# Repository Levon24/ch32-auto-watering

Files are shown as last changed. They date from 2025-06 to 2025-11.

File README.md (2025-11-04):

# ch32-auto-watering
Hello, the goal of this project was to create an automatic watering system for indoor plants using inexpensive and readily available components that can be ordered on AliExpress for final production. The system is based on the CH32v003 SoC, the most common board without a quartz crystal (at the time of writing, it costs 0.5$).
Here is device photo.
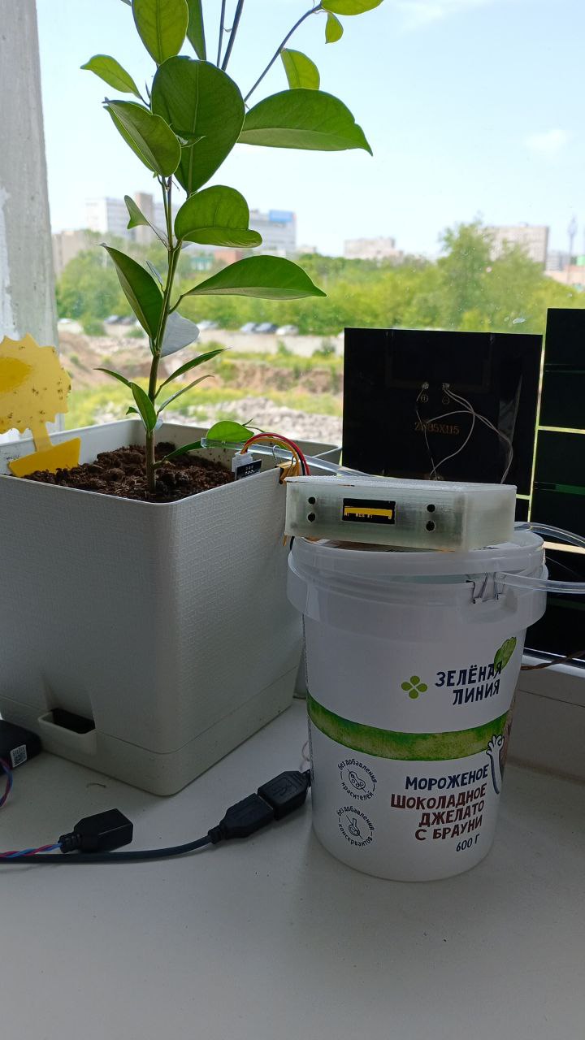
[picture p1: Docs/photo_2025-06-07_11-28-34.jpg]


## Electrical schema
The device's electrical circuit uses ready-made blocks, including a key for controlling the automatic irrigation pump. It would be better to build it using a modern element base of field-effect transistors. However, I had a lot of Soviet transistors, such as the KT601, KT602, and KT815, which I used to assemble the key for controlling the pump.
Here is main electrical schema.
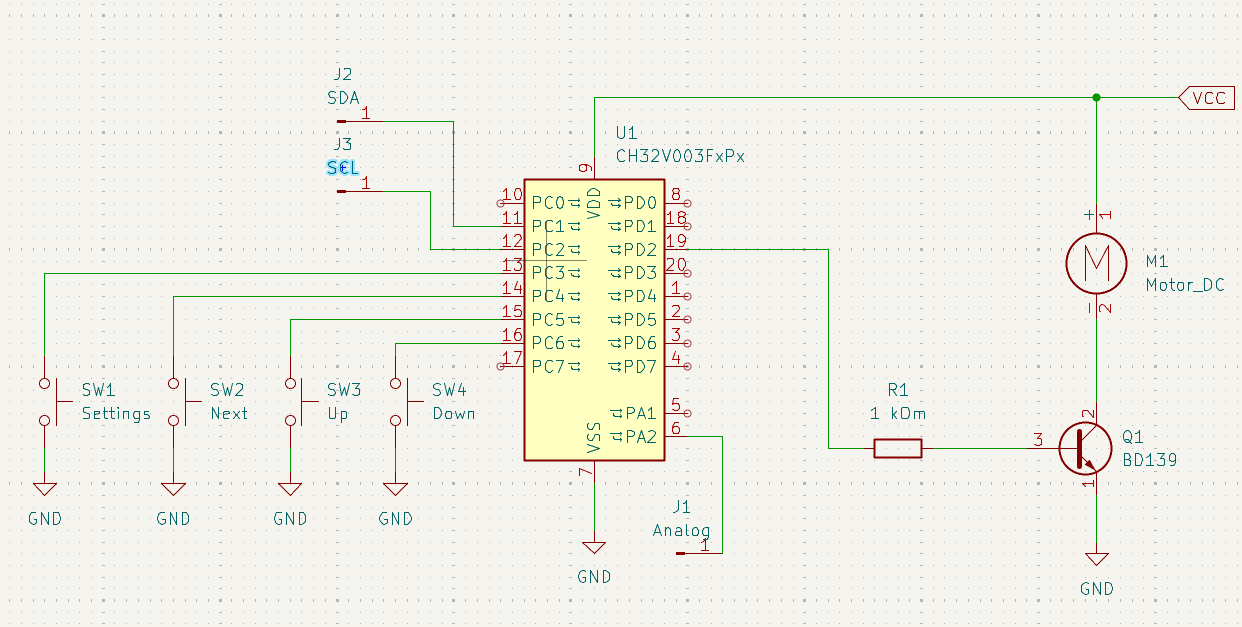
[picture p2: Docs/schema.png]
schema


As you can see in the image below, most of the prototype device is surface mounted and is not yet finished, as the project is still being refined.
Here is main block.
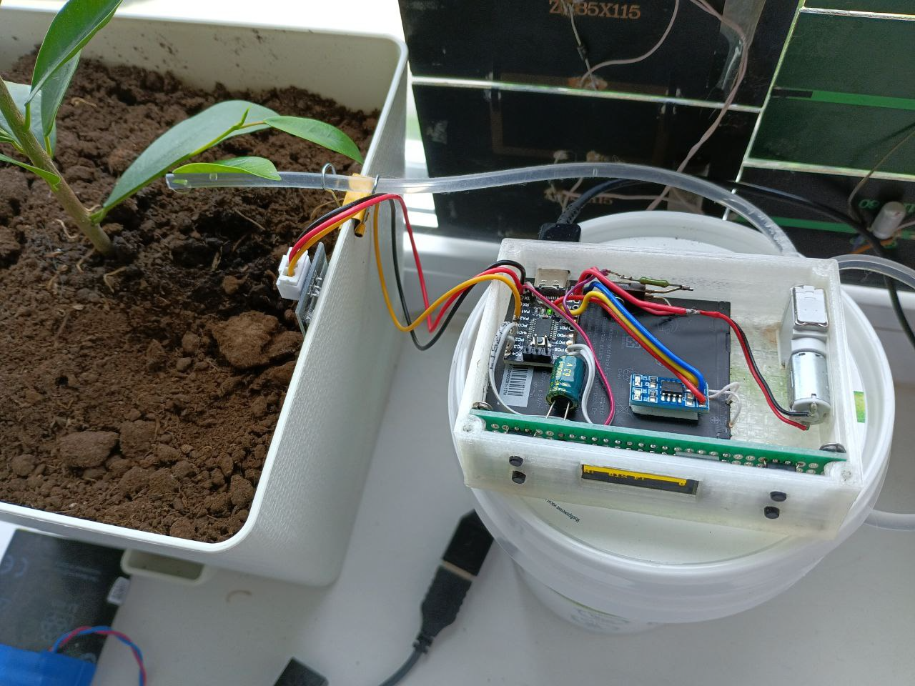
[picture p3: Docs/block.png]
block


### Soil moisture sensor
Initially, I used a common resistive soil moisture sensor for the device and, as shown in the diagram above, fed the signal to the ADC input. It was convenient for measuring data, from 0 V to a supply voltage of 3.3 V. The controller has a 10-bit ADC, so the values ranged from 0 to 1023 and were easy to convert to moisture percentages. However, something went wrong and the sensor malfunctioned.
Here is result.
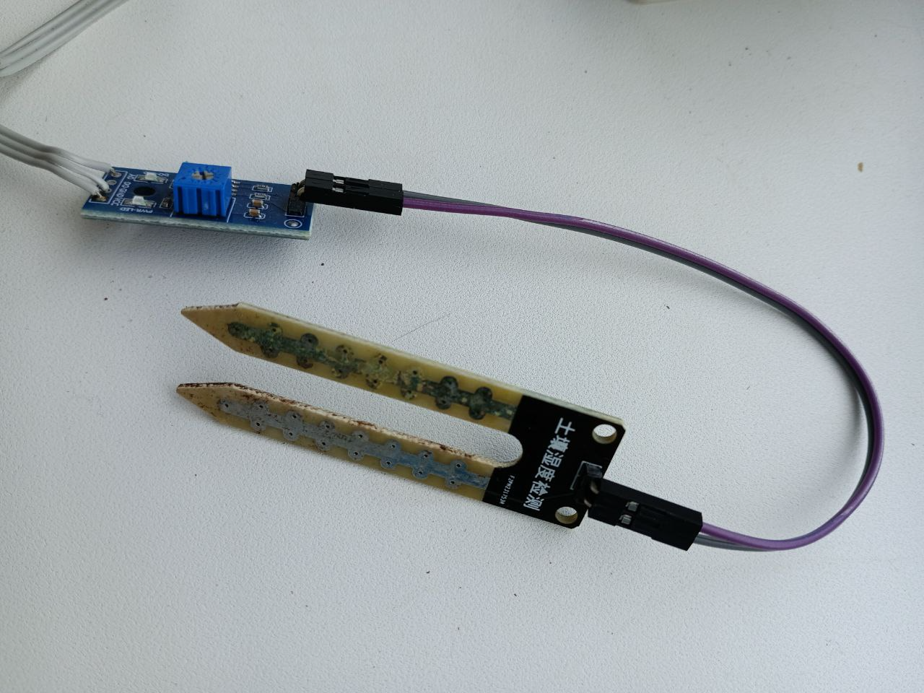
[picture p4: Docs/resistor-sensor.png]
resistor-sensor


The process of sensor electrode oxidation, as it turns out, is well-known. So, the solution is - using capacitive sensors.
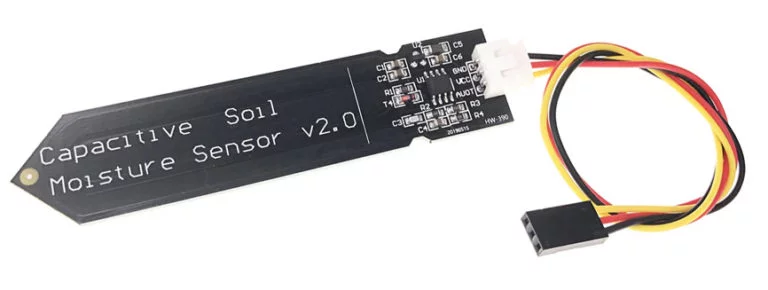
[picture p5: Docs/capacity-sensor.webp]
capacity-sensor


### Oled display
To display the data, I chose an OLED display with a 128x32 resolution. It displays current readings and a moisture graph over time. A target soil moisture value can be specified in the settings. The display shows two parameters: M (soil moisture) and F (flood value). The display itself is connected via two wires and operates using the I2C protocol.
The price of oled display 1$.
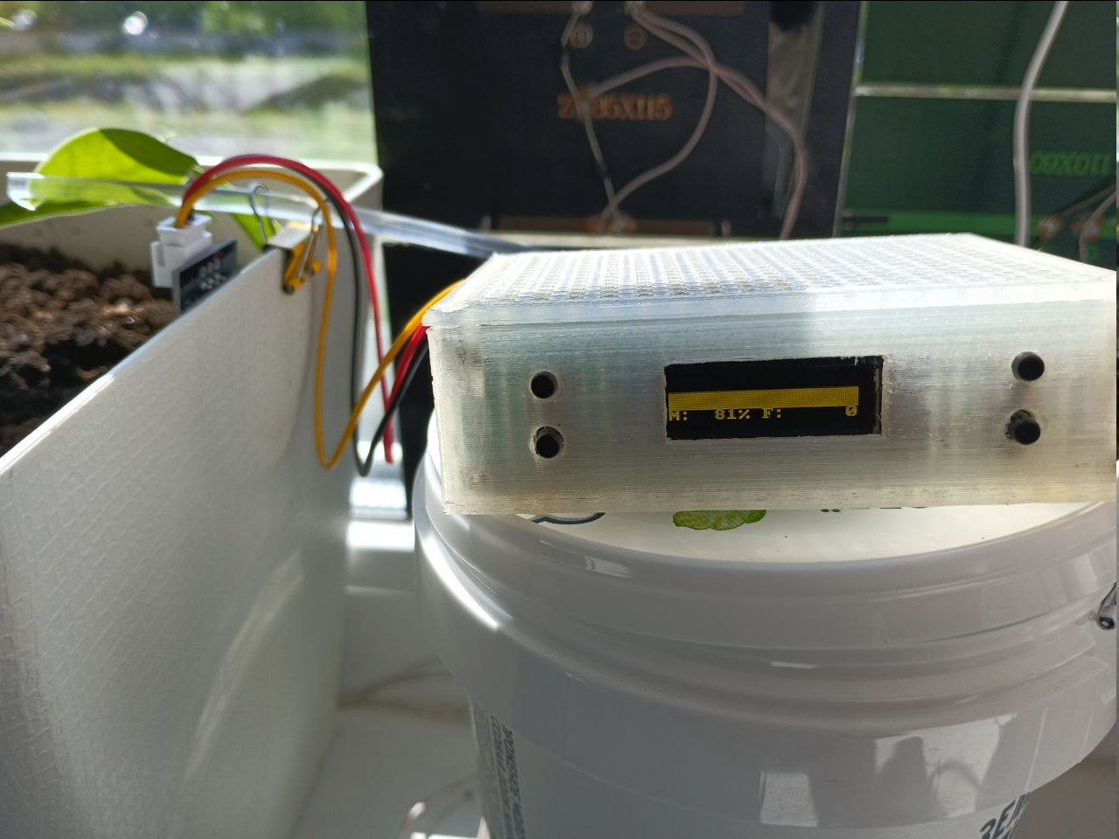
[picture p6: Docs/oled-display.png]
oled-display


### Pump
So, if the soil moisture is insufficient, the device begins to continuously dispense water until a set time threshold is reached, or until the soil reaches the desired moisture level. The time threshold is configured in the source code. I used the smallest **CJWP08** pump, which costs about 0.5$, so I set the threshold to 30 seconds of continuous watering. The pump then switches to drip mode, releasing a drop of water every set time until the desired moisture level is reached.

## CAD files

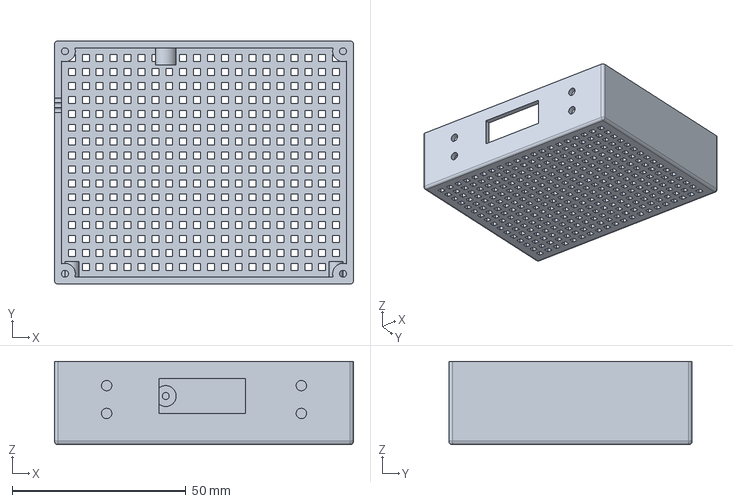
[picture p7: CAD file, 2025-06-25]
Docs/box.FCStd
86.0 x 70.0 x 24.0 mm

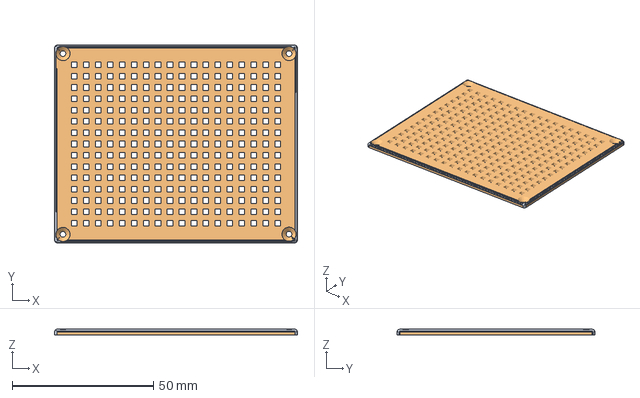
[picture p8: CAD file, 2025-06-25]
Docs/lid.FCStd
86.0 x 70.0 x 2.00 mm
MultiTransform (Meshed)

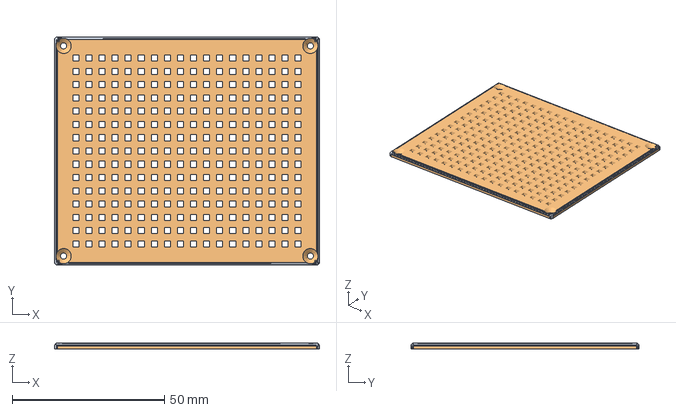
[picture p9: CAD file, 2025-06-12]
Docs/lid2.FCStd
87.0 x 75.0 x 2.00 mm
Body (Meshed)

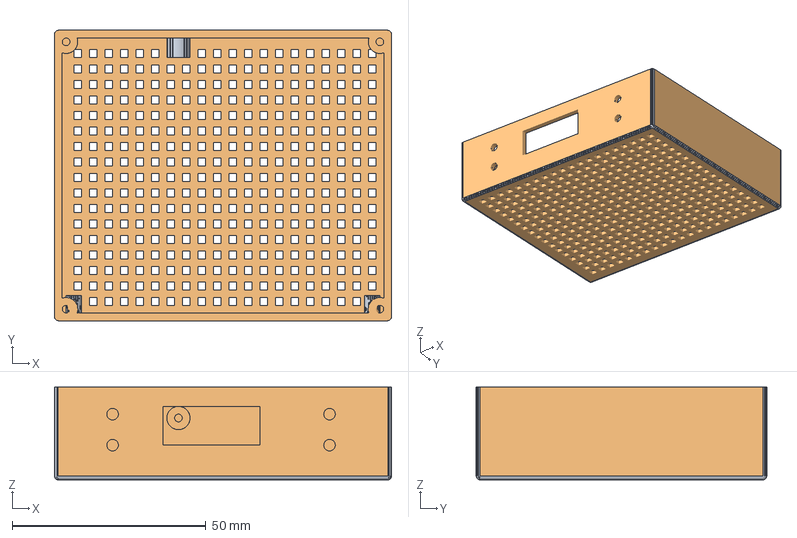
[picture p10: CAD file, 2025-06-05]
Docs/box2.FCStd
87.0 x 75.0 x 24.0 mm
Pad002 (Meshed)

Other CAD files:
Docs/box.stl
Docs/box2.stl
Docs/lid.stl
Docs/lid2.stl

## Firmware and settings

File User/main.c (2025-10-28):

#include "debug.h"
#include "display.h"
#include "fonts.h"
#include "buttons.h"

#define _TIM2_PSC   ((SystemCoreClock / 1000) - 1)
#define _TIM2_ARR   (1000 - 1)

#define SENSOR_CAP      1 // Емкостной датчик?
#define SENSOR_PIN      GPIO_Pin_0
#define PUMP_PIN        GPIO_Pin_2
#define MOISTURE        80 // Цель для влажности почвы
#define DELAY_MS        50 // Задержка в основном цикле, 20 кадров в секунду
#define FLOOD_STEP      5  // Сколько за шаг полива добавлять в счетчик потопа
#define FLOOD_MAX       (30 * FLOOD_STEP * 1000) / DELAY_MS // 30 секунд максимум лить воду до потопа
#define CHART_SECONDS   5  // Через сколько секунд график сдвигать вправо
#define CHART_SIZE      8 * 3
#define CHART_MAX       10
#define U_VREF          1.2 // 1.2V 
#define U_VCC           3.3 // 3.3V
#define U_DRY           2.26 // Калибровка для емкостного датчика 0 влажности (для v1.2 = 2.193, для v2.0 = 2.752)
#define U_WET           1.10 // Калибровка для емкостного датчика 100 влажности (для v1.2 = 1.06, для v2.0 = 1.304)

uint8_t seconds = 0;
uint8_t displayLine[128];
uint8_t chartValues[128];

extern enum display_state state;
extern enum display_setup setup;
extern _button_t buttons[BUTTONS];

extern const uint8_t font8x8[][8];
const uint8_t levels[] = {0b00000000, 0b10000000, 0b11000000, 0b11100000, 0b11110000, 0b11111000, 0b11111100, 0b11111110, 0b11111111};

uint8_t contrast = DISPLAY_DEFAULT_CONTRAST;
uint8_t moisture = 0;
uint8_t minMoisture = MOISTURE;
uint16_t flood = 0;

/**
 * @brief Init Port A
 */
void initPortA() {
  RCC_APB2PeriphClockCmd(RCC_APB2Periph_GPIOA, ENABLE);

  GPIO_InitTypeDef initTypeDef = {0};
  initTypeDef.GPIO_Pin = SENSOR_PIN;
  initTypeDef.GPIO_Mode = GPIO_Mode_AIN;
  GPIO_Init(GPIOA, &initTypeDef);
}

/**
 * @brief Init Port C
 */
void initPortC() {
  RCC_APB2PeriphClockCmd(RCC_APB2Periph_GPIOC, ENABLE);
  
  GPIO_InitTypeDef initI2C = {0};
  initI2C.GPIO_Pin = GPIO_Pin_1 | GPIO_Pin_2;
  initI2C.GPIO_Mode = GPIO_Mode_AF_OD;
  initI2C.GPIO_Speed = GPIO_Speed_30MHz;
  GPIO_Init(GPIOC, &initI2C);

  GPIO_InitTypeDef initButtons = {0};
  initButtons.GPIO_Pin = BUTTON_SETTINGS | BUTTON_NEXT | BUTTON_UP | BUTTON_DOWN;
  initButtons.GPIO_Mode = GPIO_Mode_IPU;
  initButtons.GPIO_Speed = GPIO_Speed_30MHz;
  GPIO_Init(GPIOC, &initButtons);
}

/**
 * @brief Init Port D
 */
void initPortD() {
  RCC_APB2PeriphClockCmd(RCC_APB2Periph_GPIOD, ENABLE);

  GPIO_InitTypeDef initTypeDef = {0};
  initTypeDef.GPIO_Pin = PUMP_PIN;
  initTypeDef.GPIO_Mode = GPIO_Mode_Out_PP;
  initTypeDef.GPIO_Speed = GPIO_Speed_30MHz;
  GPIO_Init(GPIOD, &initTypeDef);
}

/**
 * @brief Init I2C
 */
void initI2C() {
  RCC_APB1PeriphClockCmd(RCC_APB1Periph_I2C1, ENABLE);

  I2C_InitTypeDef initTypeDef = {0};
  initTypeDef.I2C_ClockSpeed = DISPLAY_I2C_SPEED;
  initTypeDef.I2C_Mode = I2C_Mode_I2C;
  initTypeDef.I2C_DutyCycle = I2C_DutyCycle_2;
  initTypeDef.I2C_OwnAddress1 = 0x00;
  initTypeDef.I2C_Ack = I2C_Ack_Enable;
  initTypeDef.I2C_AcknowledgedAddress = I2C_AcknowledgedAddress_7bit;
  I2C_Init(I2C1, &initTypeDef);

  I2C_Cmd(I2C1, ENABLE);
}

/**
 * @brief Init ADC
 */
void initADC() {
  RCC_ADCCLKConfig(RCC_PCLK2_Div12); // 2 MHz

  RCC_APB2PeriphClockCmd(RCC_APB2Periph_ADC1, ENABLE);
  ADC_DeInit(ADC1);

  ADC_InitTypeDef initTypeDef = {0};
  initTypeDef.ADC_Mode = ADC_Mode_Independent;
  initTypeDef.ADC_ScanConvMode = DISABLE;
  initTypeDef.ADC_ContinuousConvMode = DISABLE;
  initTypeDef.ADC_ExternalTrigConv = ADC_ExternalTrigConv_None;
  initTypeDef.ADC_DataAlign = ADC_DataAlign_Right;
  initTypeDef.ADC_NbrOfChannel = 1;
  ADC_Init(ADC1, &initTypeDef);

  ADC_Calibration_Vol(ADC1, ADC_CALVOL_50PERCENT);
  ADC_Cmd(ADC1, ENABLE);

  ADC_ResetCalibration(ADC1);
  while (ADC_GetResetCalibrationStatus(ADC1));

  ADC_StartCalibration(ADC1);
  while (ADC_GetCalibrationStatus(ADC1));
}

/**
 * @brief Init TIM2
 */
void initTIM2() {
  RCC_APB1PeriphClockCmd(RCC_APB1Periph_TIM2, ENABLE);
    
  TIM_TimeBaseInitTypeDef timInitTypeDef = {0};
  timInitTypeDef.TIM_ClockDivision = TIM_CKD_DIV1;
  timInitTypeDef.TIM_Prescaler = _TIM2_PSC;
  timInitTypeDef.TIM_Period = _TIM2_ARR;
  timInitTypeDef.TIM_CounterMode = TIM_CounterMode_Up;
  TIM_TimeBaseInit(TIM2, &timInitTypeDef);

  TIM_ITConfig(TIM2, TIM_IT_Update, ENABLE);

  NVIC_InitTypeDef nvicInitTypeDef = {0};
  nvicInitTypeDef.NVIC_IRQChannel = TIM2_IRQn;
  nvicInitTypeDef.NVIC_IRQChannelPreemptionPriority = 0;
  nvicInitTypeDef.NVIC_IRQChannelSubPriority = 1;
  nvicInitTypeDef.NVIC_IRQChannelCmd = ENABLE;
  NVIC_Init(&nvicInitTypeDef);
  
  TIM_Cmd(TIM2, ENABLE);
}

/**
 * @brief Initialization
 */
void init() {
  RCC_APB2PeriphClockCmd(RCC_APB2Periph_AFIO, ENABLE);
  
  initPortA();
  initPortC();
  initPortD();
  
  initI2C();
  initADC();

  initTIM2();
}

/**
 * @brief Get the Adc Value
 * 
 * @param channel 
 * @return uint16_t 
 */
uint16_t getAdcValue(uint8_t channel) {
  ADC_RegularChannelConfig(ADC1, channel, 1, ADC_SampleTime_241Cycles);
  ADC_SoftwareStartConvCmd(ADC1, ENABLE);
  while (!ADC_GetFlagStatus(ADC1, ADC_FLAG_EOC));
  return ADC_GetConversionValue(ADC1);
}

/**
 * @brief IRQ Timer 2
 */
void TIM2_IRQHandler(void) __attribute__((interrupt("WCH-Interrupt-fast")));
void TIM2_IRQHandler(void) {
  if (TIM_GetITStatus(TIM2, TIM_IT_Update) != RESET) {
    if (seconds < CHART_SECONDS) {
      seconds++;
    } else {
      seconds = 0;
      
      for (uint8_t p = 127; p > 0; p--) {
        chartValues[p] = chartValues[p - 1];
      }
      chartValues[0] = moisture;
    }
    
    TIM_ClearITPendingBit(TIM2, TIM_IT_Update); 
  }
}

/**
 * @brief Read sensor & calc moisture
 */
void readMoisture() {
  // read sensor
  uint16_t adcValue = getAdcValue(ADC_Channel_0);
  //printf("ADC: %d\r\n", adcValue);

  // calculate moisture
#if (SENSOR_CAP == 1)
  uint16_t adcVref = getAdcValue(ADC_Channel_Vrefint);
  float u = ((float) U_VREF / adcVref) * adcValue;
  if (u > U_DRY) {
    moisture = 0;
  } else {
    moisture = ((U_DRY - u) * 100) / (U_DRY - U_WET);
  }
#else
  moisture = (1023 - adcValue) / 10;
#endif
}

/**
 * @brief pump control
 */
void turnPump() {
  if (moisture < minMoisture && flood < FLOOD_MAX) {
    GPIO_WriteBit(GPIOD, PUMP_PIN, Bit_SET);
    flood = flood + FLOOD_STEP;
  } else {
    GPIO_WriteBit(GPIOD, PUMP_PIN, Bit_RESET);
  }

  if (flood > 0) {
    flood--;
  }
}

/**
 * @brief display graf
 */
void showChart() {
  char buff[17];
  
  for (uint8_t position = 0; position < 3; position++) {
    for (uint8_t p = 0; p < 128; p++) {
      uint8_t value = chartValues[p];

      uint8_t maxValue = minMoisture + CHART_MAX;
      if (value > maxValue) {
        value = maxValue;
      }

      uint8_t minValue = maxValue - CHART_SIZE;
      if (value < minValue) {
        value = minValue;
      }

      value = value - minValue;

      if (value > (2 - position) * 8) {
        uint8_t level = value - (2 - position) * 8;
        if (level > 8) {
          level = 8;
        }
        displayLine[p] = levels[level];
      } else {
        displayLine[p] = 0;
      }
    }
    displaySendData(position, displayLine, sizeof(displayLine));
  }

  sprintf(buff, "M: %3d%% F: %5d", moisture, flood);
  text(buff, displayLine);
  displaySendData(3, displayLine, sizeof(displayLine));

  if (buttons[settings].pressed > 0) {
    state = show_settings;
  }
}

/**
 * @brief display settings
 */
void showSettings() {
  char buff[17];

  text(" -= Settings =- ", displayLine);
  displaySendData(0, displayLine, sizeof(displayLine));

  sprintf(buff, "%s Moisture: %3d", (setup == setup_min_moisture ? ">" : " "), minMoisture);
  text(buff, displayLine);
  displaySendData(1, displayLine, sizeof(displayLine));

  sprintf(buff, "%s Contrast: %3d", (setup == setup_contrast ? ">" : " "), contrast);
  text(buff, displayLine);
  displaySendData(2, displayLine, sizeof(displayLine));

  clear(displayLine, sizeof(displayLine));
  displaySendData(3, displayLine, sizeof(displayLine));

  if (buttons[settings].pressed > 0) {
    state = show_chart;
  }

  if (buttons[next].pressed > 0) {
    if (setup < setup_contrast) {
      setup++;
    } else {
      setup = setup_min_moisture;
    }
  }

  if (buttons[up].pressed > 0) {
    switch (setup) {
      case setup_min_moisture:
        if (minMoisture < 100) {
          minMoisture++;
        }
        break;

      case setup_contrast:
        if (contrast < 0xFF) {
          contrast++;
          displaySetContrast(contrast);
        }
        break;
    }
  }

  if (buttons[down].pressed > 0) {
    switch (setup) {
      case setup_min_moisture:
        if (minMoisture > 0) {
          minMoisture--;
        }
        break;

      case setup_contrast:
        if (contrast > 0) {
          contrast--;
          displaySetContrast(contrast);
        }
        break;
    }
  }
}

/*********************************************************************
 * @fn      main
 *
 * @brief   Main program.
 *
 * @return  none
 */
int main(void) {
  NVIC_PriorityGroupConfig(NVIC_PriorityGroup_1);
  SystemCoreClockUpdate();
  Delay_Init();

#if (SDI_PRINT == SDI_PR_OPEN)
  SDI_Printf_Enable();
#else
  USART_Printf_Init(115200);
#endif

  printf("SystemClk: %d\r\n", SystemCoreClock);
  printf("ChipID: %08x\r\n", DBGMCU_GetCHIPID());

  init();
  displayInit();

  while (1) {
    readMoisture();
    turnPump();

    buttons_scan();
    switch (state) {
      case show_chart:
        showChart();
        break;
      
      case show_settings:
        showSettings(); 
        break;
    }
    
    Delay_Ms(DELAY_MS);
  }
}

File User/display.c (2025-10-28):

#include <stdio.h>
#include <ch32v00x.h>
#include "display.h"

enum display_state state = show_chart;
enum display_setup setup = setup_min_moisture;

/**
 * Send data to display
 * 
 * @param data 
 * @param size 
 */
void displaySend(uint8_t command, uint8_t *data, uint8_t size) {
  while (I2C_GetFlagStatus(I2C1, I2C_FLAG_BUSY) != RESET) {
    //printf("I2C_FLAG_BUSY\r\n");
  }
  
  I2C_GenerateSTART(I2C1, ENABLE);
  while (!I2C_CheckEvent(I2C1, I2C_EVENT_MASTER_MODE_SELECT)) {
    //printf("I2C_EVENT_MASTER_MODE_SELECT\r\n");
  }

  I2C_Send7bitAddress(I2C1, DISPLAY_I2C_ADDRESS, I2C_Direction_Transmitter);
  while (!I2C_CheckEvent(I2C1, I2C_EVENT_MASTER_TRANSMITTER_MODE_SELECTED)) {
    //printf("I2C_EVENT_MASTER_TRANSMITTER_MODE_SELECTED\r\n");
  }

  I2C_SendData(I2C1, command);
  while (!I2C_CheckEvent(I2C1, I2C_EVENT_MASTER_BYTE_TRANSMITTED)) {
    //printf("I2C_EVENT_MASTER_BYTE_TRANSMITTED\r\n");
  }

  for (uint8_t p = 0; p < size; p++) {
    I2C_SendData(I2C1, *data);
    data++;

    while (!I2C_CheckEvent(I2C1, I2C_EVENT_MASTER_BYTE_TRANSMITTED)) {
      //printf("I2C_EVENT_MASTER_BYTE_TRANSMITTED\r\n");
    }
  }
  
  I2C_GenerateSTOP(I2C1, ENABLE);
}

/**
 * Send byte to display
 * 
 * @param byte 
 */
void displaySendCommand(uint8_t command) {
  displaySend(0, &command, 1);
}

/**
 * Initialization
 */
void displayInit() {
  // Set MUX Ratio A8h, 3Fh
  // Set Display Offset D3h, 00h
  // Set Display Start Line 40h
  // Set Segment re-map A0h/A1h
  // Set COM Output Scan Direction C0h/C8h
  // Set COM Pins hardware configuration DAh, 02
  // Set Contrast Control 81h, 7Fh
  // Disable Entire Display On A4h
  // Set Normal Display A6h
  // Set Osc Frequency D5h, 80h
  // Enable charge pump regulator 8Dh, 14h
  // Display On AFh

  Delay_Ms(100);

  displaySendCommand(SSD1306_DISPLAY_OFF);

	displaySendCommand(SSD1306_SET_DISPLAY_CLOCK_DIV);
  displaySendCommand(0x00);
  
  displaySendCommand(SSD1306_SET_MULTIPLEX);
  displaySendCommand(SSD1306_MULTIPLEX_128_32);

  displaySendCommand(SSD1306_SET_DISPLAY_OFFSET);
  displaySendCommand(0x00);

  displaySendCommand(SSD1306_SET_START_LINE | 0x00);

  displaySendCommand(SSD1306_CHARGE_PUMP);
  displaySendCommand(0x14); // Enable Charge Pump

  displaySendCommand(SSD1306_MEMORY_MODE);
  displaySendCommand(0x00); // Horizontal addressing mode (A[1:0]=00b)
  
  displaySendCommand(SSD1306_SEG_REMAP_YES);
	
  displaySendCommand(SSD1306_COM_SCAN_DEC); // Flip?

	displaySendCommand(SSD1306_SET_COM_PINS);
  displaySendCommand(0x02); //for 128x32 0x02, for 128x64 0x12;

  displaySendCommand(SSD1306_DEACTIVATE_SCROLL);

  displaySendCommand(SSD1306_COLUMN_ADDR);
  displaySendCommand(0x00);
  displaySendCommand(0xFF);

  displaySendCommand(SSD1306_PAGE_ADDR);
  displaySendCommand(0x00);
  displaySendCommand(0x07);

	displaySendCommand(SSD1306_SET_CONTRAST);
	displaySendCommand(DISPLAY_DEFAULT_CONTRAST);

	//displaySendCommand(SSD1306_SET_PRE_CHARGE);
	//displaySendCommand(0xF1);

	displaySendCommand(SSD1306_SET_V_COM_DETECT);
	displaySendCommand(0x40);

	displaySendCommand(SSD1306_DISPLAY_ALLON_RESUME);

	displaySendCommand(SSD1306_DISPLAY_ON);
}

void displaySetCursor(uint8_t x, uint8_t y) {
	// Y - 1 unit = 1 page (8 pixel rows)
	// X - 1 unit = 8 pixel columns

	displaySendCommand(0x00 | (8 * x & 0x0F)); 		      // Set column lower address
	displaySendCommand(0x10 | ((8 * x >> 4) & 0x0F));   // Set column higher address
	displaySendCommand(0xB0 | y);                       // Set page address
}

void displaySendData(uint8_t page, uint8_t *data, uint8_t size) {
	//displaySendCommand(SSD1306_PAGE_ADDR);
	//displaySendCommand(0x00);
	//displaySendCommand(0x07);

	displaySendCommand(SSD1306_SET_PAGE_START_ADDRESS | page);
	displaySendCommand(SSD1306_SET_HIGHER_COLUMN_START_ADDRESS);
	displaySendCommand(SSD1306_SET_LOWER_COLUMN_START_ADDRESS);

	displaySend(SSD1306_SET_START_LINE, data, size);
}

void displaySetContrast(uint8_t value) {
	displaySendCommand(SSD1306_SET_CONTRAST);
	displaySendCommand(value);
}

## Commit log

2025-04-06 Add i2c init
2025-04-09 Init i2c scanner
2025-04-24 Fix bug with print
    [main.c]
2025-04-28 Add new sensor type
2025-04-29 Add switch for different sensors
2025-04-30 move debug info to uart
2025-05-03 Change adc model
2025-05-26 Add box
    [box.FCStd, box.stl]
2025-05-28 Fix box
    [box.FCStd, box.stl]
2025-06-02 Add lid
    [box.FCStd, box.stl, box2.FCStd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]
2025-06-02 Add schema
    [schema.kicad_pcb, schema.kicad_sch]
2025-06-05 Added v2 for box
    [box2.FCStd, box2.stl]
2025-06-12 Add lid2
    [lid2.FCStd, lid2.stl]
2025-06-18 Updated box v1.0
    [box.FCStd, box.stl]
2025-06-25 Update lid
    [box.FCStd, lid.FCStd, lid.stl]
2025-06-27 Some calibrations
2025-07-09 Add adc mesures
    [adc.ods]
2025-07-10 Speedup pumping
2025-10-28 Has been updates buttons logic
2025-10-28 Some updates
    [adc.ods]
